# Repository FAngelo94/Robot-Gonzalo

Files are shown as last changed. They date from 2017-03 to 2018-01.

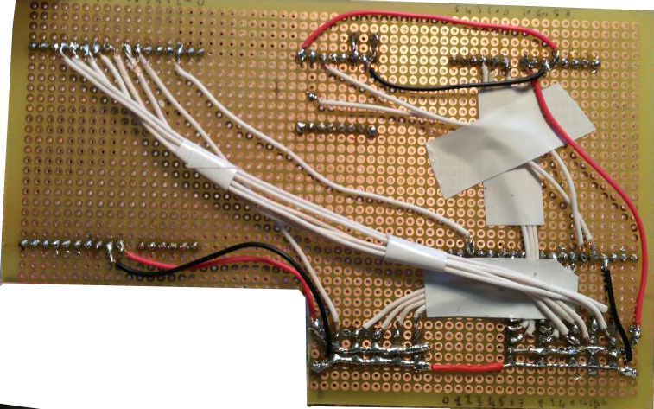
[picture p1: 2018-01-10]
Final presentation-20170502T090655Z-001/Gonzalo/photos/foto modificate/IMG-20170406-WA0012modif.png

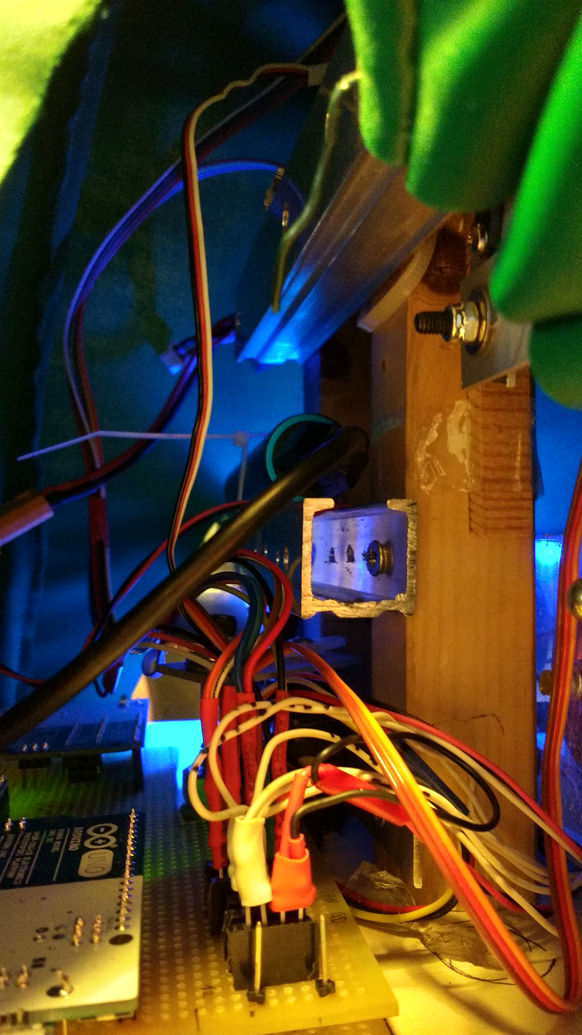
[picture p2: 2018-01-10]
Final presentation-20170502T090655Z-001/Gonzalo/photos/IMG_20170501_154248415_HDR.jpg

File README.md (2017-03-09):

# Robot-Gonzalo
MAIN LINK

Led RGP: http://www.maffucci.it/2014/09/27/arduino-lezione-09-uso-di-led-rgb-parte-1/

Master-Slave: https://www.arduino.cc/en/Tutorial/MasterWriter

Master-Slave between 1 master and more slaves: http://www.logicaprogrammabile.it/comunicazione-tra-arduino-tramite-i2c/

Master-Slave (Master read slave message): https://www.arduino.cc/en/Tutorial/MasterReader

DFPlayer Mini: https://www.dfrobot.com/wiki/index.php/DFPlayer_Mini_SKU:DFR0299

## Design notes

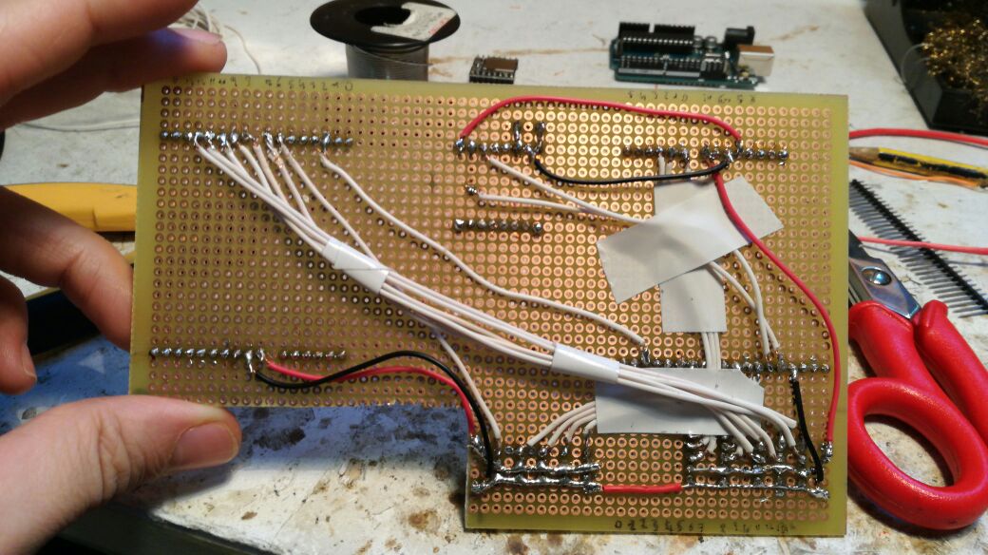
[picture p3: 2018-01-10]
Final presentation-20170502T090655Z-001/Gonzalo/photos/IMG-20170406-WA0012.jpg

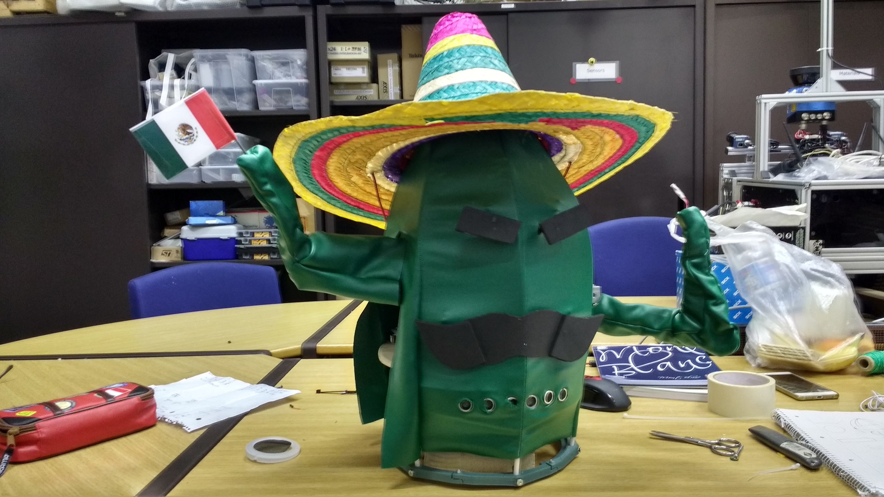
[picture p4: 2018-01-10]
Final presentation-20170502T090655Z-001/Gonzalo/photos/IMG_20170428_194357332_HDR(1).jpg

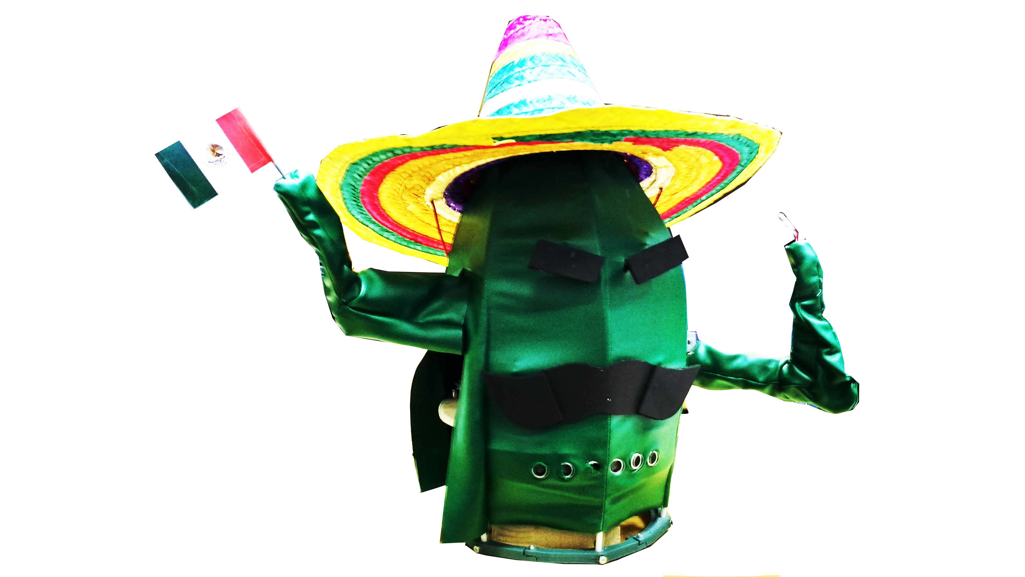
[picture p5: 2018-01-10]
Final presentation-20170502T090655Z-001/Gonzalo/photos/foto modificate/IMG_20170428_194357332_HDRmodif.jpg

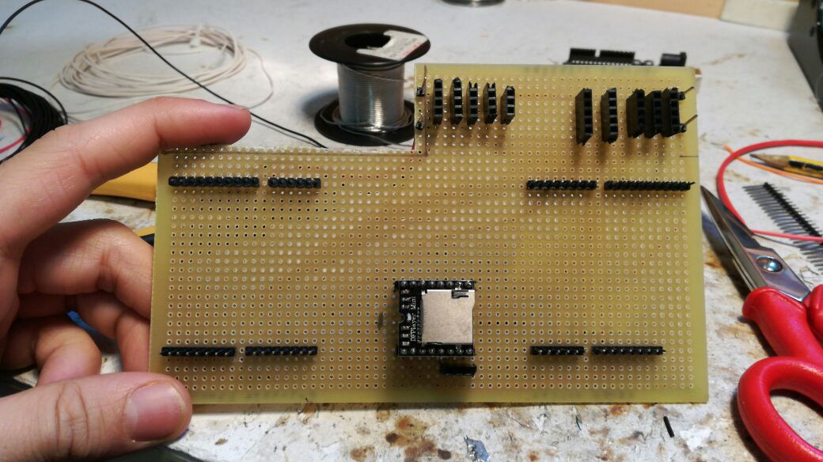
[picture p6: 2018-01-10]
Final presentation-20170502T090655Z-001/Gonzalo/photos/IMG-20170406-WA0014.jpg

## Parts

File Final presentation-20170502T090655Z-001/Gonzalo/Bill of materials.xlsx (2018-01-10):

Area | Part | quantity | Price | Total
Design
 | 3D Plastic | 1 | €25.00 | €25.00
 | Rod | 3 | €10.00 | €30.00
 | Eyes | 2 | €1.50 | €3.00
 | Fabric | 3 | €2.33 | €7.00
 | Magnets | 6 | €2.70 | €16.20
 | Various | 1 | €14.00 | €14.00
 | Foam | 1 | €5.00 | €5.00
 | Silicone | 1 | €3.00 | €3.00
 | Painting | 1 | €3.00 | €3.00
 | Inside pieces | 1 | €20.00 | €20.00
 | Cup | 2 | €0.90 | €1.80
Mechanics
 | Beams of steel | 1 | €1.00 | €1.00
 | Pulleys | 4 | €0.40 | €1.60
 | Screws | 20 | €0.10 | €2.00
 | Vase | 1 | €2.00 | €2.00
 | Ball bearing | 1 | €2.00 | €2.00
Electronics
 | LM137 | 3 | €1.40 | €4.20
 | Cables | 3 | €4.00 | €12.00
 |  |  | Final Total: | €152.80

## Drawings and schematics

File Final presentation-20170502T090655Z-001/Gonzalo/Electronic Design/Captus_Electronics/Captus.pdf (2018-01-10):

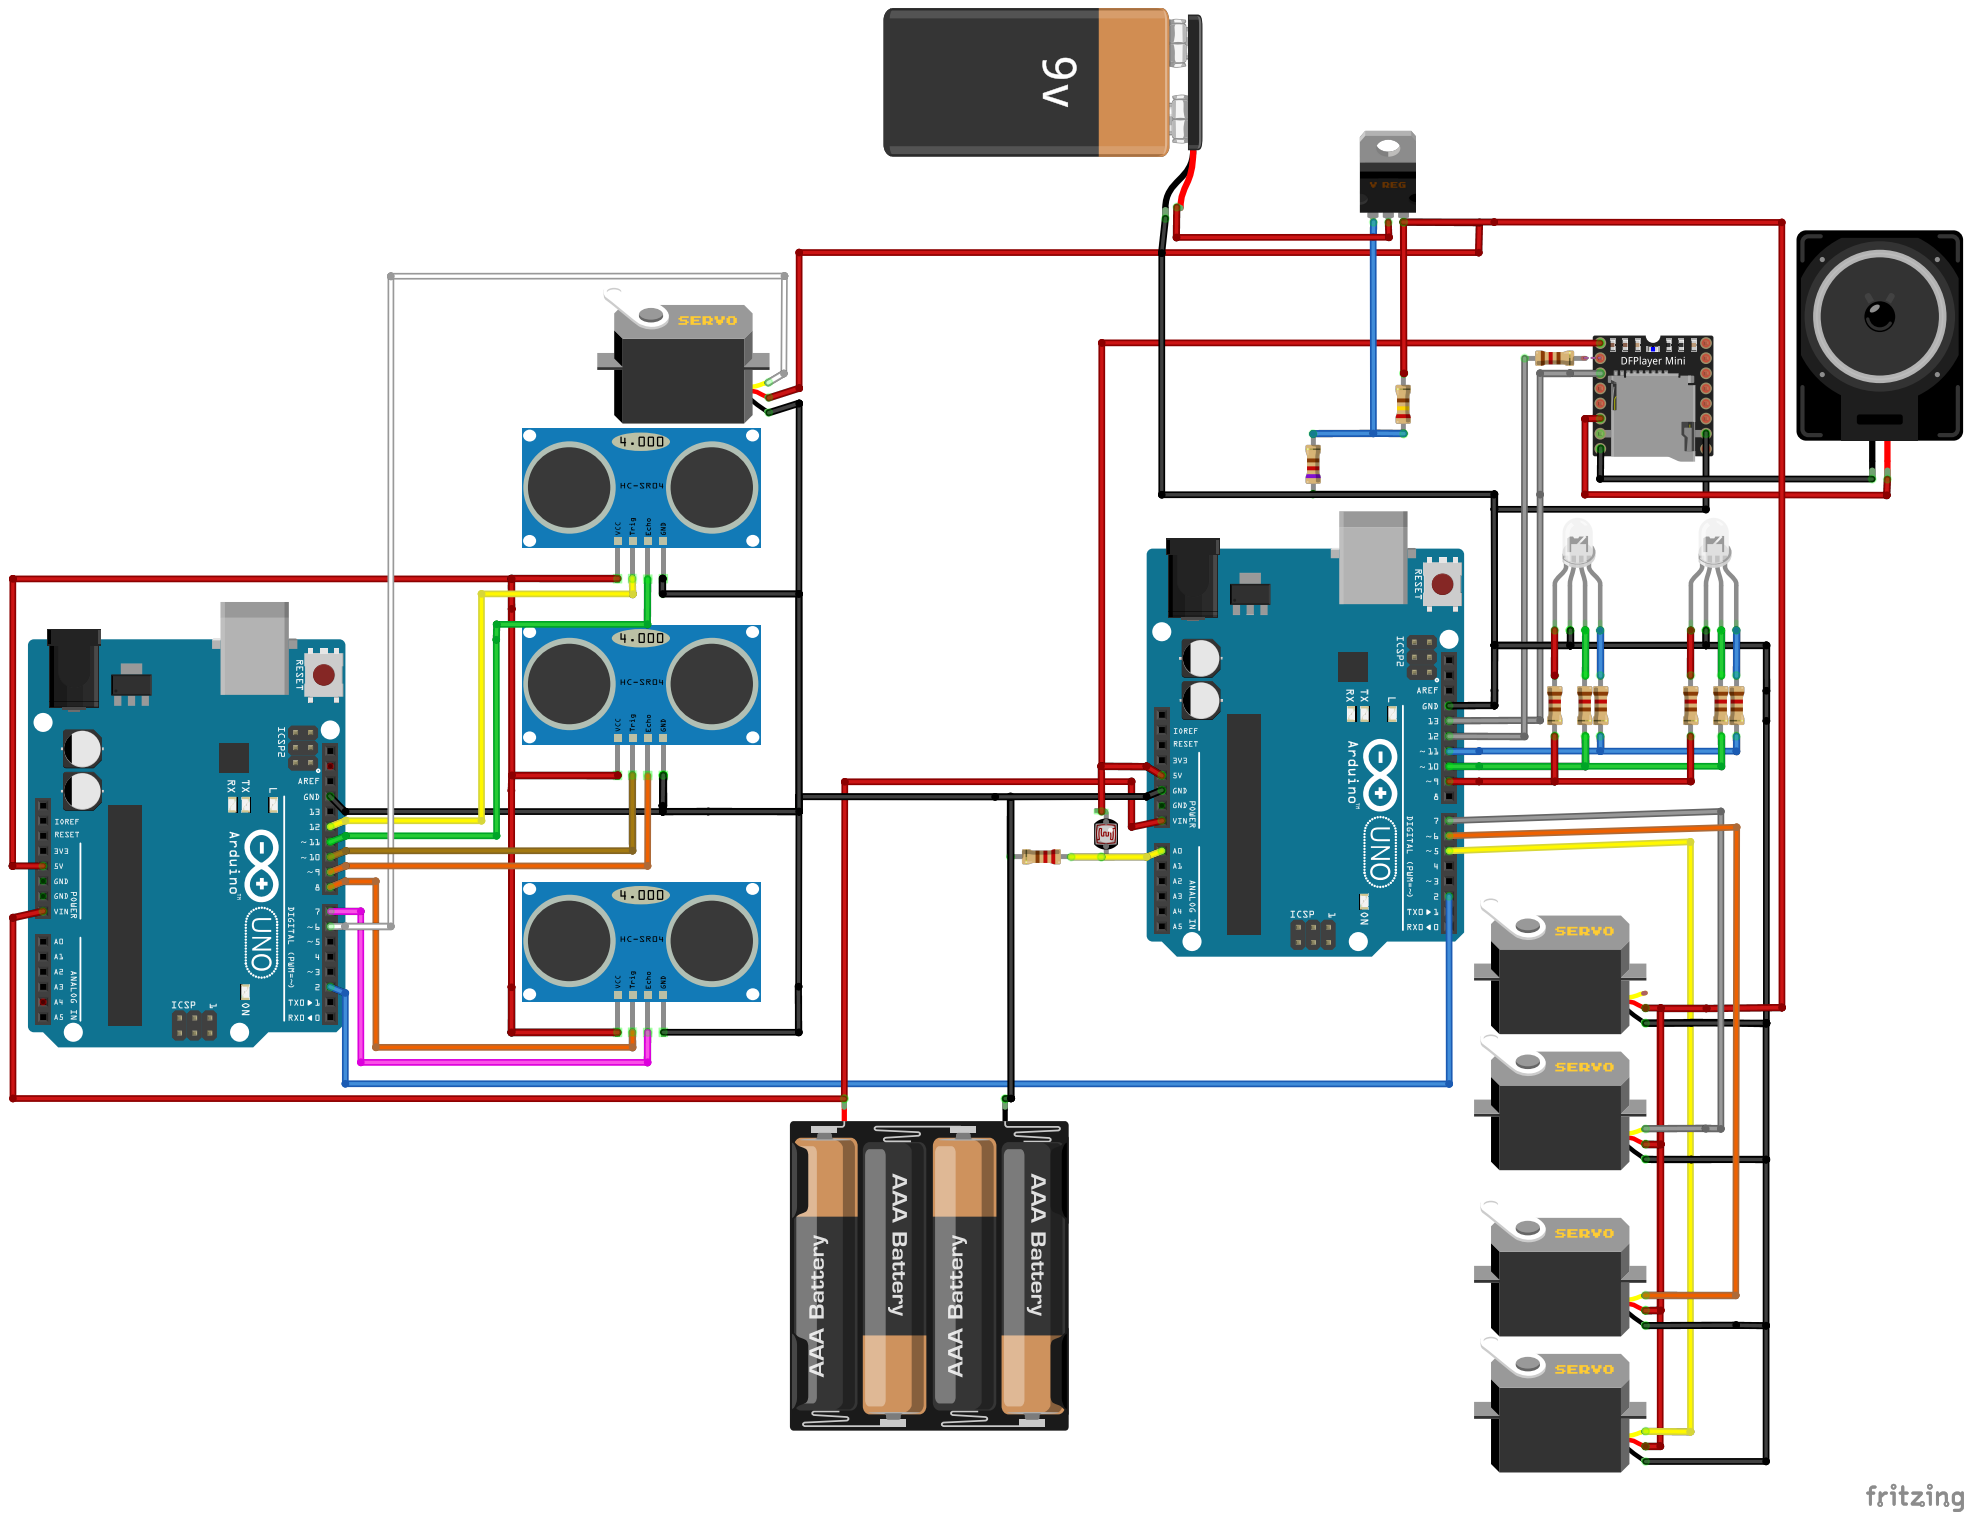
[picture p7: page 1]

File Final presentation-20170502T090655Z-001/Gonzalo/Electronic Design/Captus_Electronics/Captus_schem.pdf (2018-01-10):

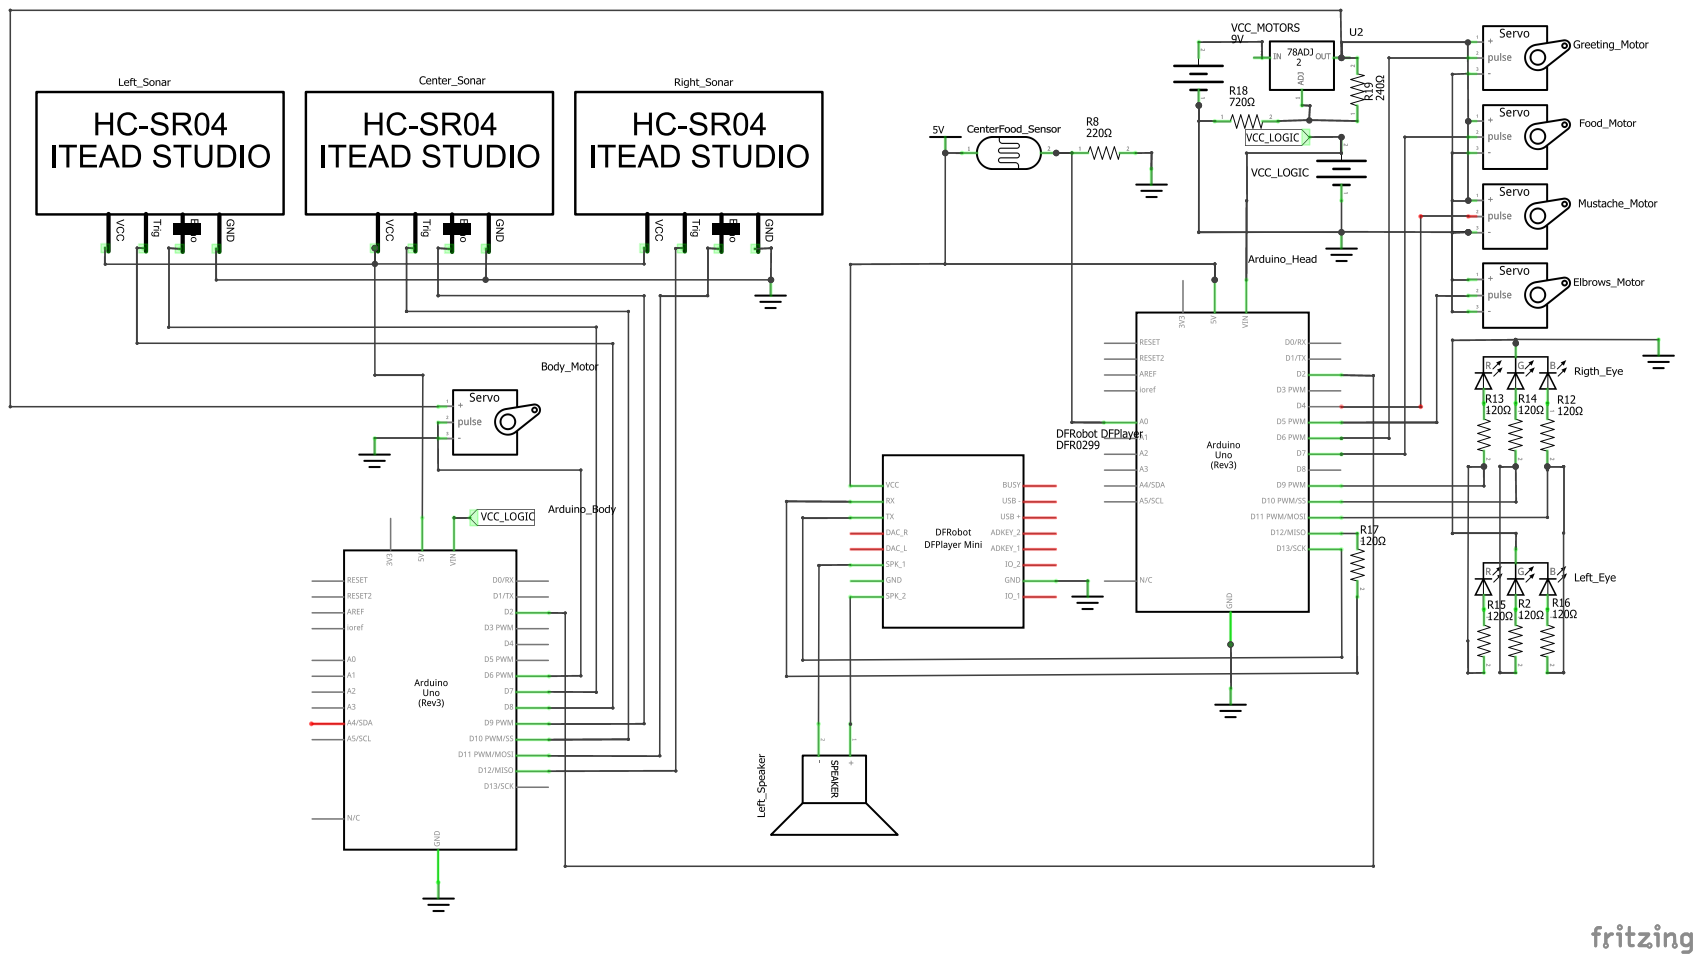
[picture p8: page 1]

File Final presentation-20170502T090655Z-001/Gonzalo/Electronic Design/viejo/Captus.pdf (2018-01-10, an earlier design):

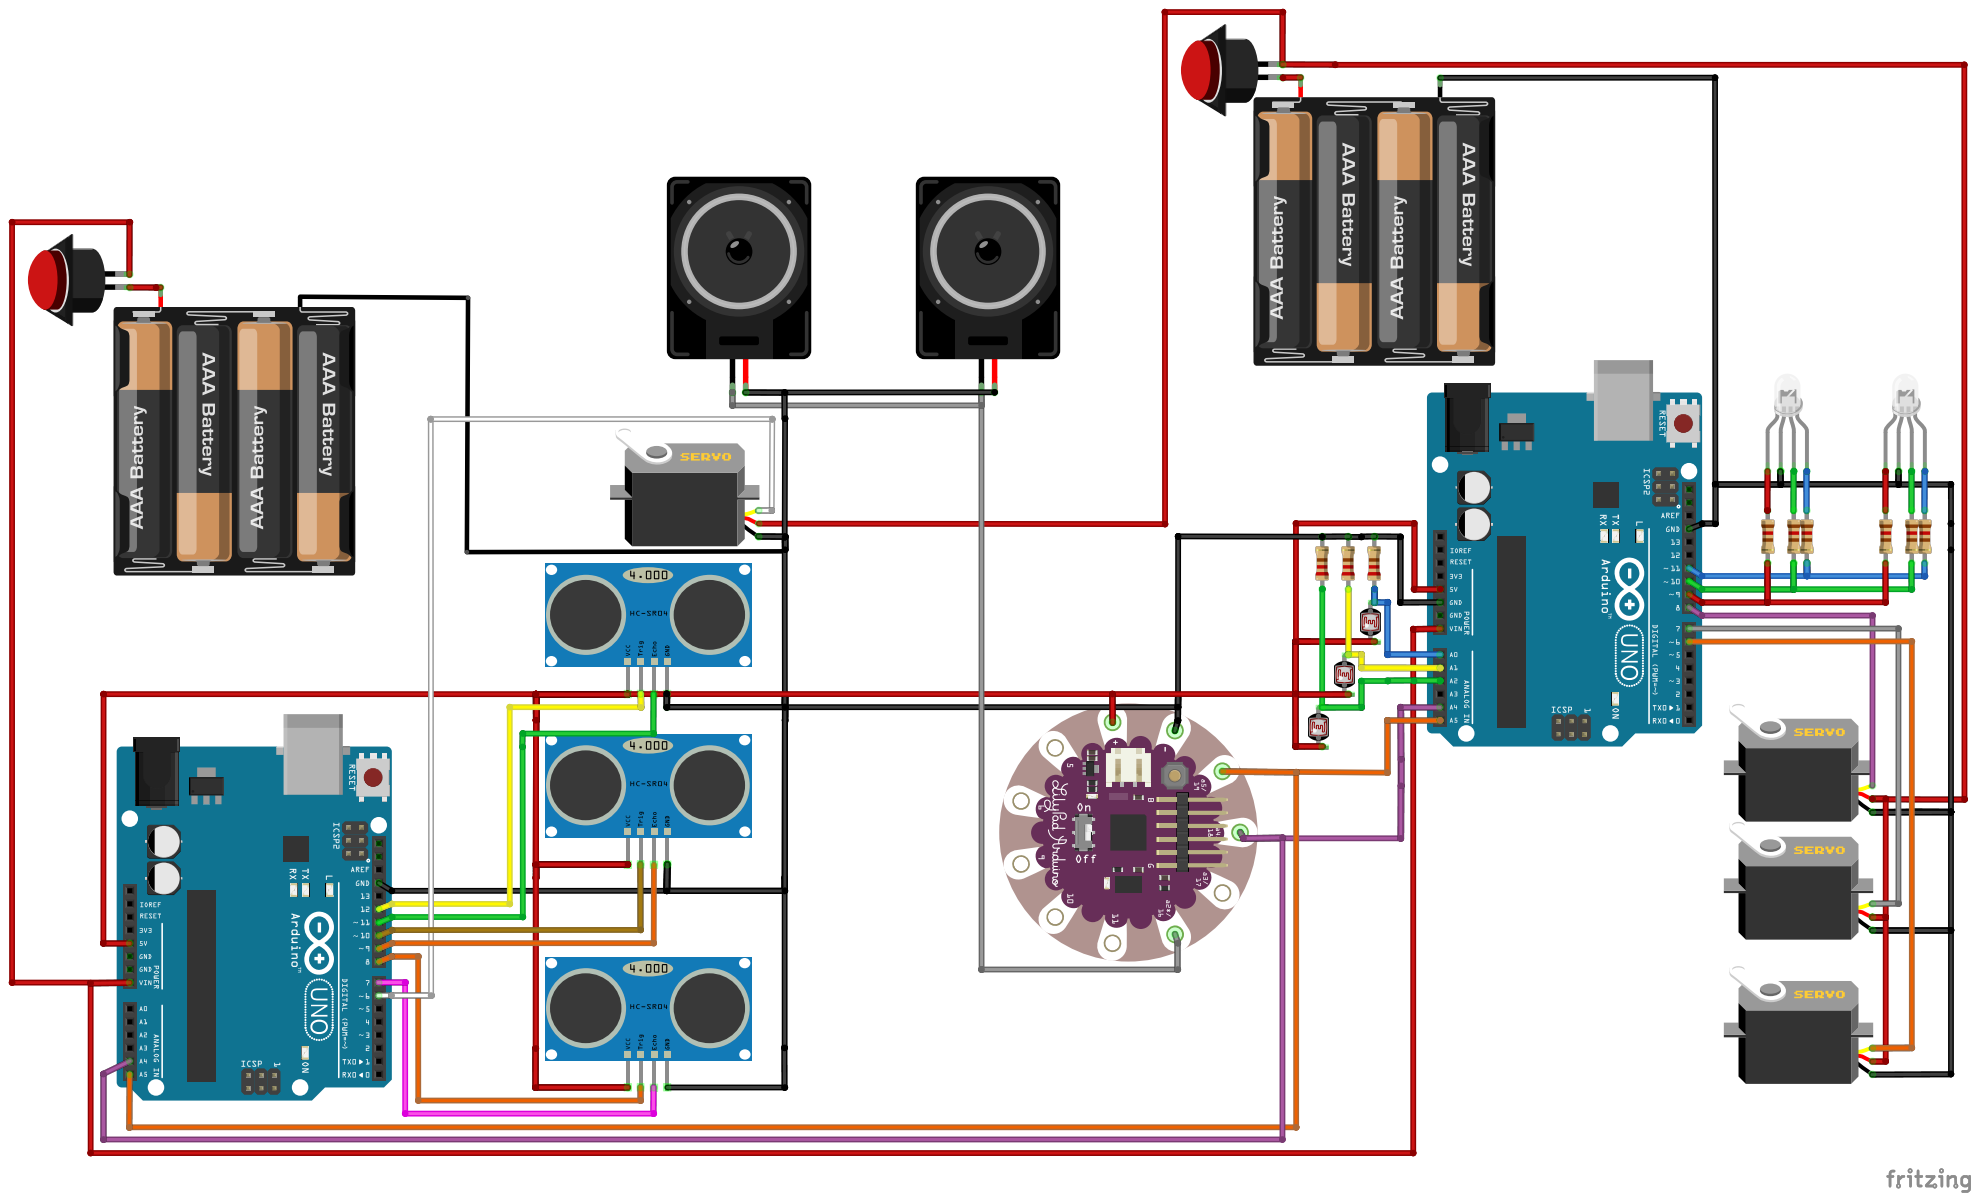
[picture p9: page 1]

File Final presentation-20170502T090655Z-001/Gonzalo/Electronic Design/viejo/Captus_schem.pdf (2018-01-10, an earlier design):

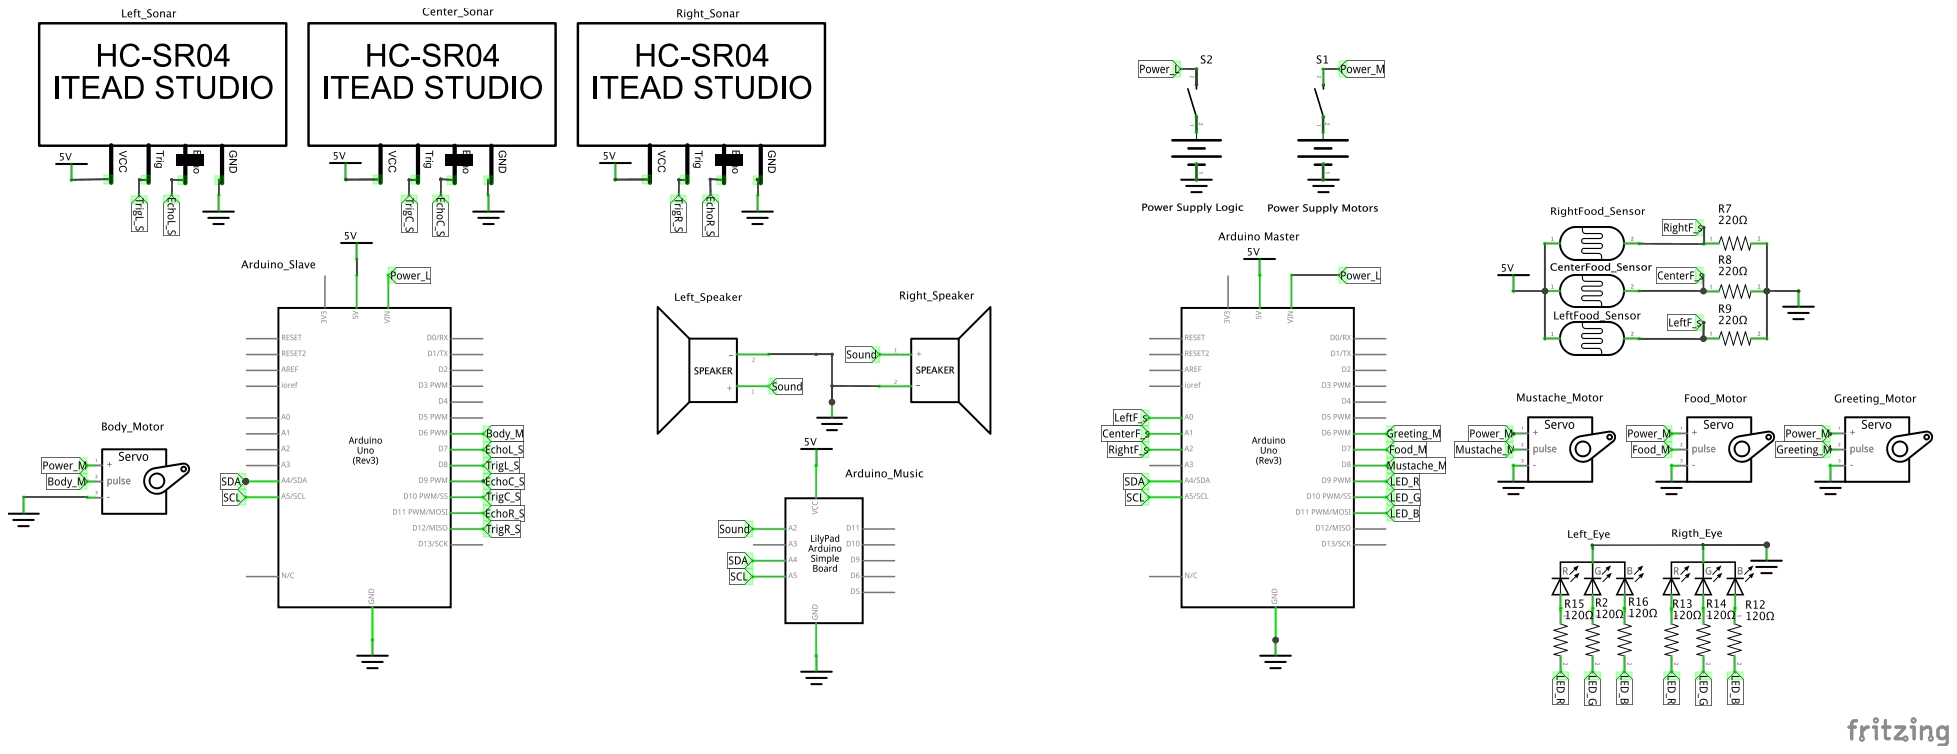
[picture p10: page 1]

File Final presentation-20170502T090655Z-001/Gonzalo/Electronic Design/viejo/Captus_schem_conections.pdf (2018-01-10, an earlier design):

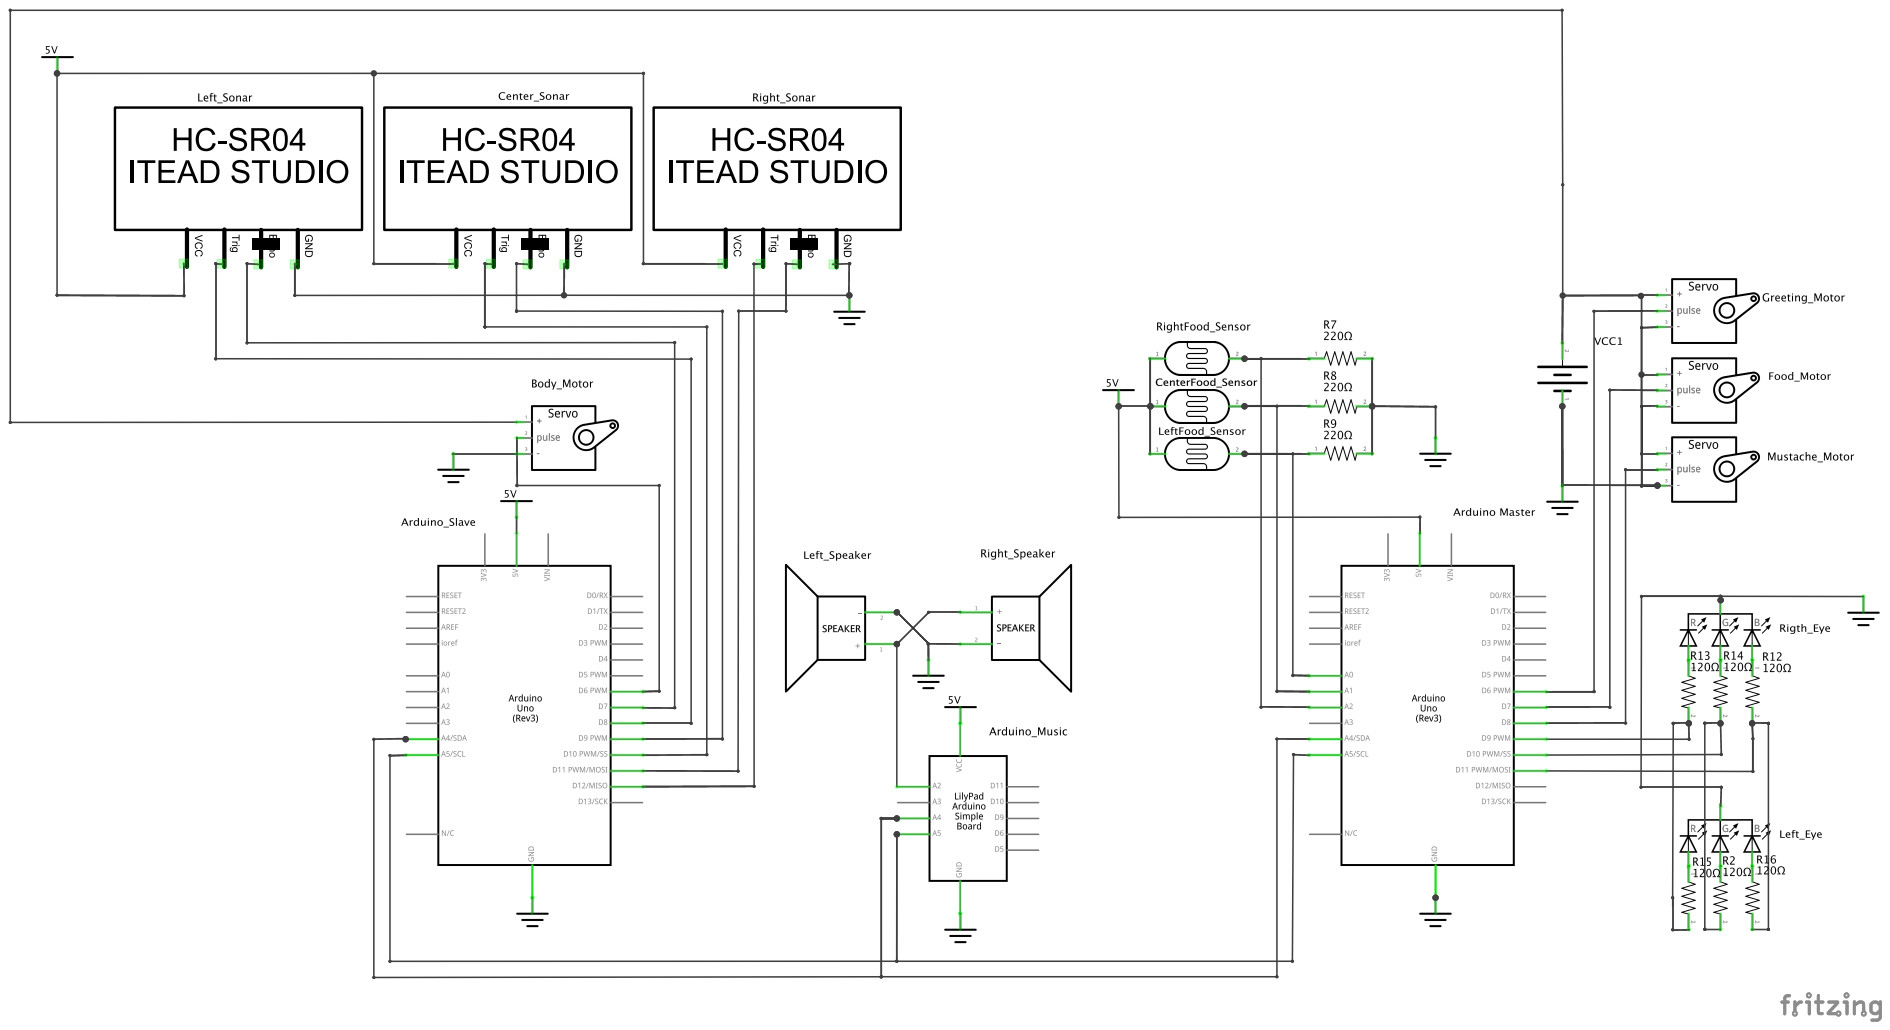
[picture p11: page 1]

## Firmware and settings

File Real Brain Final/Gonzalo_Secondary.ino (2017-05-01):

/*
 * Angelo Falci 
 * Emanuele Schiavon
 * Valentina Favaro
 * Julian Gallego
 * Soheil Ghanbari
 */
#include <Servo.h>
#include <DFRobotDFPlayerMini.h>7
#include <SoftwareSerial.h>
#include "Arduino.h"
#include "SoftwareSerial.h"
#include "DFRobotDFPlayerMini.h"

//HAND WITH FOOD
#define FOOD_PIN 7
#define PIN_SENSOR_1 A0
#define PIN_SENSOR_2 A1
#define PIN_SENSOR_3 A2
Servo foodHand;
int positionFoodHand;
long foodTime;
long rechargeFoodTime;//when food hand moved then it doesn't work for a while
boolean foodMoveFast;
boolean resetFoodHand;
//boolean foodMoveFastActive;
int oldValue[10];
int newValue;
boolean activeFoodHand;

//HELLO HAND
#define HELLO_PIN 6
Servo helloHand;
int positionHelloHand;
long helloTime;
long helloInterval;
int helloDirection;
long rechargeHi;
boolean enter;

//eyes
#define GREEN 9
#define BLU 10
#define RED 11

//speak
SoftwareSerial mySoftwareSerial(12, 13); // RX, TX
DFRobotDFPlayerMini myDFPlayer;
int enterCount;

//face
#define face1 5
#define face2 4
Servo eyeBrown, mustache;
long mustacheTime;
long mustacheDirection;
long mustacheInterval;
int mustachePosition;

//Pause
boolean sleep;

void setup() {
  //HAND WITH FOOD
  positionFoodHand=170;
  foodHand.attach(FOOD_PIN);
  foodHand.write(positionFoodHand); 
  foodMoveFast=false;
  resetFoodHand=false;
  foodTime=0;
  rechargeFoodTime=0;
  activeFoodHand=false;
  for(int i=0;i<10;i++)
  {
    oldValue[i]=analogRead(PIN_SENSOR_1);
    delay(50);
  }
  //HELLO HAND
  positionHelloHand=90;
  helloHand.attach(HELLO_PIN);
  helloHand.write(positionHelloHand);
  helloTime=0;
  helloInterval=0;
  helloDirection=0;
  rechargeHi=0;
  enter=false;
  //eye setup
  pinMode(GREEN, OUTPUT);  
  pinMode(BLU, OUTPUT);  
  pinMode(RED, OUTPUT);
  blueEye();
  //Set up mustache
  eyeBrown.attach(face1);
  mustache.attach(face2);
  eyeBrown.write(90);
  mustache.write(90);
  mustacheTime=-3000;
  mustacheDirection=0;
  mustacheInterval=0;
  mustachePosition=90;
  sadMustache();
  delay(2000);
  helloHand.detach();
  eyeBrown.detach();
  mustache.detach();
  foodHand.detach();
  helloTime=millis();
  //Body Arduino send in pin 2 the signal when a person is detected in front of it
  pinMode(2, INPUT);
  //Set up the DF Player
  mySoftwareSerial.begin(9600);
  enterCount=0;
  //Serial.begin(115200);
  
  if (!myDFPlayer.begin(mySoftwareSerial)) {  //Use softwareSerial to communicate with mp3.
    while(true);
  }
  myDFPlayer.volume(10);  //Set volume value. From 0 to 304
  sleep=false;
}

void loop() {
  checkDistance();
  moveHandFast();
  sayhi();
  laughMustache();
  sadMustache();
}
//Check if the signal of "near person" is activated or not
void checkDistance(){
   
    if(digitalRead(2)==HIGH)
    {
      //Serial.println("CIAO");
        helloTime=millis();
        activeFoodHand=true;
    }
}

//MOVE FAST THE HAND IF A PERSON TRY TO KEEP FOOD
//When someone try to keep food Gonzalo move hand, say "ahahah" and move mustache to laugh for about 2 second,
//and then his hand return in the original position
void moveHandFast()
{
  
  //Serial.println(foodMoveFast);
  long diff=millis()-rechargeFoodTime;
  if(foodMoveFast==false && millis()-foodTime>=200 && diff>0)
  {
    double maxL=0;
    for(int i=0;i<10;i++)
      if(oldValue[i]>maxL)
        maxL=oldValue[i];
    double diff=((double)newValue-(double)maxL)/((double)maxL)*100;
    newValue=analogRead(PIN_SENSOR_1);
    
    /*Serial.print("FOTO=");
    Serial.print(newValue);
    Serial.print(" - ");
    Serial.println(maxL);
    Serial.print("DIF=");
    Serial.println(diff);*/
    
    if(diff<-15 && activeFoodHand==true)
    {//A person is trying to take food
      foodMoveFast=true;
      activeFoodHand=false;
      redEye();
    }
    else
    {
      for(int i=0;i<9;i++)
        oldValue[i]=oldValue[i+1];
      oldValue[9]=newValue;
    }
    foodTime=millis();
  }
  if(foodMoveFast==true)
  {
      
      if(helloHand.attached())
        helloHand.detach();
       
      rechargeHi=millis()+5000; //After move hand fast Gonzalo don't say hi for a while
      foodHand.attach(FOOD_PIN);
      for(int i=170;i>120;i=i-3)
      {
        foodHand.write(i);
        delay(15);
      }
      foodHand.detach();
      speak("fun");
      mustacheTime=millis();
      foodMoveFast=false;
      resetFoodHand=true;
      foodTime=millis();
      rechargeFoodTime=millis()+10000;//After move hand fast Gonzalo don't move the food hand again for a while
      
  }
  if(resetFoodHand==true && rechargeFoodTime-millis()<5000)
  {
    for(int i=0;i<10;i++)
    {
      oldValue[i]=analogRead(PIN_SENSOR_1);
      delay(20);
    }
    foodHand.attach(FOOD_PIN);
      for(int i=120;i<170;i++)
      {
        foodHand.write(i);
        delay(20);
      }
      foodHand.detach();
      resetFoodHand=false;
    normalMustache();
    blueEye();
  }
}

//Robot say hi for 3 seconds when the body arduino give the signal
void sayhi()
{ 
  long diff=millis()-rechargeHi;
  if(millis()-helloTime<3000 && millis()-helloInterval>10 && helloTime!=0 && diff>0 && enter==false)
  {
    //Serial.println("sto salutando");
  if(!helloHand.attached() || sleep==true)  
  {
    if(!helloHand.attached()) 
      helloHand.attach(HELLO_PIN);
    happyMustache();
    speak("hi");
    greenEye();
  }
  if(helloDirection==0)
    {
      positionHelloHand=positionHelloHand+2;
      if(positionHelloHand>=110)
      {
        helloDirection=1;
      }
    }
    else
    {
      positionHelloHand=positionHelloHand-2;
      if(positionHelloHand<=70)
      {
        helloDirection=0;
      }
    } 
  helloHand.write(positionHelloHand);
  helloInterval=millis();
  }
  if(millis()-helloTime>=3000 && helloHand.attached() && sleep==false)
  {//detach the servo when Gonzalo not say hello
    
    if(helloHand.attached())
      helloHand.detach();
    rechargeHi=millis()+8000;
    enter=true;
  }
  if(millis()-helloTime>=5000 && sleep==false)
  {//detach the servo when Gonzalo not say hello
    blueEye();
  }
  if(millis()-helloTime<3000 && millis()-helloInterval>20 && helloTime!=0 && diff>0 && enter==true)
  {
    if(helloHand.attached())
      helloHand.detach();
      normalMustache();
    speak("enter");
    helloTime=millis()-3000;
    rechargeHi=millis()+5000;
    enter=false;
  }
}

void blueEye()
{
  digitalWrite(GREEN, LOW);  
  digitalWrite(BLU, LOW);  
  digitalWrite(RED, HIGH);
}
void redEye()
{
  digitalWrite(GREEN, HIGH);  
  digitalWrite(BLU, LOW);  
  digitalWrite(RED, LOW);
}
void greenEye()
{
  digitalWrite(GREEN, LOW);  
  digitalWrite(BLU, HIGH);  
  digitalWrite(RED, LOW);
}

//MANAGE ROBOT SPEAKING
void speak(String s)
{
  if(s=="enter")
  {
    if(enterCount==0)
      myDFPlayer.play(2);
    if(enterCount==1)
      myDFPlayer.play(5);
    if(enterCount==2)
      myDFPlayer.play(6);
    enterCount++;
    if(enterCount>2)
    enterCount=0;
  }
  if(s=="song")
  {
    myDFPlayer.play(1);  
  }
  if(s=="hi")
  {
    myDFPlayer.play(3); 
  }
  if(s=="fun")
  {
    myDFPlayer.play(4); 
  }
}

//MANAGE EYEBROW AND MUSTACHE
void normalMustache()
{
  if(!eyeBrown.attached())
    eyeBrown.attach(face1);
  if(!mustache.attached())
    mustache.attach(face2);

  eyeBrown.write(90);
  mustache.write(90);
  delay(200);
  
  eyeBrown.detach();
  mustache.detach(); 
}

void happyMustache()
{
  if(!eyeBrown.attached())
    eyeBrown.attach(face1);
  if(!mustache.attached())
    mustache.attach(face2);

  eyeBrown.write(20);
  mustache.write(150);
  delay(200);
  
  eyeBrown.detach();
  mustache.detach(); 
}
//default position when there isn't anyone
//Gonzalo become sad when it doesn't interact with anyone for a while
void sadMustache()
{
  long dist1=millis()-helloTime;
  long dist2=millis()-rechargeFoodTime;
  if(!(dist1>10000 && dist2>0))
    sleep=false;
  if(dist1>10000 && dist2>0)
  {
    if(!mustache.attached())
      mustache.attach(face2);
    if(mustacheDirection==0)
    {
      mustachePosition=mustachePosition+1;
      if(mustachePosition>120)
        mustacheDirection=1;
    }
    else
    {
      mustachePosition=mustachePosition-1;
      if(mustachePosition<60)
        mustacheDirection=0;
    }
    mustache.write(mustachePosition);
    if(!helloHand.attached())  
    {
      helloHand.attach(HELLO_PIN);
      normalMustache();
      speak("song");
      sleep=true;
    }
    if(helloDirection==0)
    {
      positionHelloHand=positionHelloHand+1;
      if(positionHelloHand>=110)
      {
        helloDirection=1;
      }
    }
    else
    {
      positionHelloHand=positionHelloHand-1;
      if(positionHelloHand<=70)
      {
        helloDirection=0;
      }
    } 
    if(!helloHand.attached())  
      helloHand.attach(HELLO_PIN);
    helloHand.write(positionHelloHand);
    delay(10);
  }
}
void laughMustache()
{
  if(millis()-mustacheTime<5000 && millis()-mustacheInterval>10)
  {
    if(!eyeBrown.attached())
    {
      eyeBrown.attach(face1);
      delay(10);
      eyeBrown.write(160);
    }
    if(!mustache.attached())
      mustache.attach(face2);
    if(mustacheDirection==0)
    {
      mustachePosition=mustachePosition+4;
      if(mustachePosition>120)
        mustacheDirection=1;
    }
    else
    {
      mustachePosition=mustachePosition-4;
      if(mustachePosition<60)
        mustacheDirection=0;
    }
    mustache.write(mustachePosition);
    mustacheInterval=millis();
  }
  if(millis()-mustacheTime>500)
  {
    if(eyeBrown.attached())
      eyeBrown.detach();
  }
  if(millis()-mustacheTime>5000)
  {
    if(mustache.attached())
      mustache.detach();
  }
}

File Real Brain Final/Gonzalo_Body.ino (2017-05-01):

/*
 * Servo Gonzalo
 * This arduino manage the sonar and movements of body
 */
#include <Servo.h>
#include <NewPing.h>

#define MAX_DISTANCE 400 // Maximum distance we want to ping for (in centimeters). Maximum sensor distance is rated at 400-500cm.

#define TRIGGER_PIN1  12  // Arduino pin tied to trigger pin on the ultrasonic sensor.
#define ECHO_PIN1     11  // Arduino pin tied to echo pin on the ultrasonic sensor.

#define TRIGGER_PIN2  10  // Arduino pin tied to trigger pin on the ultrasonic sensor.
#define ECHO_PIN2    9  // Arduino pin tied to echo pin on the ultrasonic sensor.

#define TRIGGER_PIN3  8  // Arduino pin tied to trigger pin on the ultrasonic sensor.
#define ECHO_PIN3    7  // Arduino pin tied to echo pin on the ultrasonic sensor.

//Right
NewPing right(TRIGGER_PIN1, ECHO_PIN1, MAX_DISTANCE); // NewPing setup of pins and maximum distance.
//Center
NewPing center(TRIGGER_PIN2, ECHO_PIN2, MAX_DISTANCE); // NewPing setup of pins and maximum distance.
//Left
NewPing left(TRIGGER_PIN3, ECHO_PIN3, MAX_DISTANCE); // NewPing setup of pins and maximum distance.
//distance of every sonar
int distR[3], distL[3], distC[3];
double sonarTime;
//Servo for the rotation and its position
#define BODY_PIN 6
Servo bodyMotor;

//Variable to manage Hello
long helloTime;

int r,c,l;
static int MAX=3;

void setup() {
  //BODY
  Serial.begin(9600);
  bodyMotor.attach(BODY_PIN);
  bodyMotor.write(90);
  delay(500);
  bodyMotor.detach();
  for(int i=0;i<MAX;i++)
  {
    distR[i]=right.ping_median();
    distR[i]=right.convert_cm(distR[i]);
  }
  delay(30);
  for(int i=0;i<MAX;i++)
  {
    distC[i]=center.ping_median();
    distC[i]=center.convert_cm(distC[i]);
  }
  delay(30); 
  for(int i=0;i<MAX;i++)
  {
    distL[i]=left.ping_median(); 
    distL[i]=left.convert_cm(distL[i]);
  }
  //Set up hello
  helloTime=0;
  c=400;
  pinMode(2, OUTPUT);
  digitalWrite(2, LOW);
  delay(1000);
}
void loop() {
  checkSonar();
  /*Serial.print("CCCCCCC=");
  Serial.println(c);*/
  if(millis()-helloTime>=4000 && (c<170 && c!=0))
  {
    Serial.println("CIAO");
    sayHello();
    helloTime=millis();
  }
}

//MANAGE SONAR AND ROTATION OF ROBOT
void checkSonar()
{
  for(int i=0;i<MAX;i++)
    distR[i]=distR[i+1];
  distR[MAX-1]=right.ping_median(5);
  distR[MAX-1]=right.convert_cm(distR[MAX-1]);
  //delay(30);
  for(int i=0;i<MAX;i++)
    distC[i]=distC[i+1];
  distC[MAX-1]=center.ping_median(5);
  distC[MAX-1]=center.convert_cm(distC[MAX-1]);
  //delay(30);
  for(int i=0;i<MAX;i++)
    distL[i]=distL[i+1]; 
  distL[MAX-1]=left.ping_median(5); 
  distL[MAX-1]=left.convert_cm(distL[MAX-1]);
  Serial.print("VR=");
  Serial.print(distR[MAX-1]);
  Serial.print(" - ");
  
  Serial.print("VC=");
  Serial.print(distC[MAX-1]);
  Serial.print(" - ");
  
  Serial.print("VL=");
  Serial.println(distL[MAX-1]);
  //delay(30);
  r=distR[MAX-1],c=distC[MAX-1],l=distL[MAX-1];
  if(distR[MAX-1]==0 || distC[MAX-1]==0 || distL[MAX-1]==0)
  {
    for(int i=0;i<MAX;i++)
    {
      if(distR[i]!=0)
        r=distR[i];
      if(distC[i]!=0)
        c=distC[i];
      if(distL[i]!=0)
        l=distL[i];
    }
  }
  Serial.print("R=");
  Serial.print(r);
  Serial.print(" - ");
  
  Serial.print("C=");
  Serial.print(c);
  Serial.print(" - ");
  
  Serial.print("L=");
  Serial.println(l);
  
  if(r==0)
    r=400;
  if(c==0)
    c=400;
  if(l==0)
    l=400;
  if(c<20)//if there is someone in front of him he doesn't do useless movement
    return; 
  
  bodyMotor.attach(BODY_PIN);
  if(r+20<c && r+20<l){
    int angolo=60;
    if(r<120)
      angolo=40;
    if(r<100)
      angolo=30;
    for(int i=0;i<angolo;i++)
    {
      if(bodyMotor.read()>30)
        bodyMotor.write(bodyMotor.read()-1);
      else 
        break;
      delay(20);
    }
    
  }
  if(l+20<c && l+20<r){
    int angolo=60;
    if(l<120)
      angolo=40;
    if(l<100)
      angolo=30;
    for(int i=0;i<angolo;i++)
    {
      if(bodyMotor.read()<130)
        bodyMotor.write(bodyMotor.read()+1);
      else
        break;
      delay(20);
    }
  }
  bodyMotor.detach();
  /*Serial.print("Ping1: ");
  Serial.print(distR ); // Send ping, get distance in cm and print result (0 = outside set distance range)
  
  Serial.print("Ping2: ");
  Serial.print(distC ); // Send ping, get distance in cm and print result (0 = outside set distance range)
  
  Serial.print("Ping3: ");
  Serial.println(distL ); // Send ping, get distance in cm and print result (0 = outside set distance range)*/
}

void sayHello()
{
  /*
   * Send to the secondary arduino the command to say hello
   */
  digitalWrite(2,HIGH);
  delay(300);
  digitalWrite(2,LOW);
}

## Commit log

2017-03-09 Programma che gestisce solo i sonar
2017-03-09 Led RGP per occhi
    esempio su come usare un led rgb
2018-01-10 upload final presentation
    [Bill of materials.xlsx, Captus.fzz]
